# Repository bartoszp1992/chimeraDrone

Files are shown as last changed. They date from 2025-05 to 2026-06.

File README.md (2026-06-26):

# BD1 "Chimera" repo

**Chimera is 2,2" / 3" cinewhoop or freestyle type drone, for 3S/4S batteries, with fully 3D printed construction**

*Speed can be reduced in edgeTX system using logical switch based on the speed read from GNSS, and the mix function. The project includes a configuration that limits the speed when SB is UP*

## 3D printing

All on 0.4 brass nozzle, make sure you have at least 5 pieces- CF filaments will wear off quickly. Trim Z-offset after every CF print

I don't recommend using SS nozzle becouse it's too cold for my printer.

### tips/info
>please use proper materials. Drone components will be hot or very hot. Printing parts with PLA or similar will cause melt your construction during flight. **If my cheap Sidewinder X4 printer can handle this materials- yours printer also can.**

>It's not cheap project- don't do it because of lack of funds. Buying a ready frame will be cheaper than buying CF filaments

>one battery for one 2-3 minutes flight. Make sure you have more than 1

### parts
- **ducts**
: PA12. after print heat and bend down the wing trims by 90 degrees
- **frame**
: PC-CF/PETG-CF, 2 wall loops, no supports, 100% grid infill, rotate 15deg in Z axis
- **body**
: PA12
- **wings**
: any
- **roof**
: TPU A95
- **GNSS mount**
: TPU A95
- **Grip nuts, sleeves**
: PETG
- **top lock**
: PETG
- **light plate**
: TPU
- **bumper**
: PP
- **motor screw shim**
: PC

## BOM

### 3D printed
- 1 x ducts
- 1 x body
- 1 x frame
- 1 x left wing
- 1 x right wing
- 1 x roof or mount roof
- 1 x GNSS mount
- 1 x top lock
- 2 x camera sleeves
- 4 x sleeve 2mm
- 4 x sleeve 3mm
- 4 x grip nuts
- 1 x light plate
- 16 x 1.2mm sleeve for frame30
- 16 x 0.6mm sleeve for frame22

### electronic
- [ ] **FC**
: GEPRC TAKER G4 35A AIO
>you can use any other 35A+, compatible with 3/4S and 25,5mm pitch
- [ ] **propellers 2.2"**
: GEMFAN 2218 3-blade / HQprop 2216 3-blade (1.5mm shaft)
- [ ] **motors 2.2"**
: BETAFPV Lava series 1104 7200KV
- [ ] **propellers 3"**
: HQPROP T3X1.8X3 / HQPROP T3X3
- [ ] **motors 3"**
: flyfishRC FLASH 1404 4500KV
- [ ] **receiver**
: SpeedyBee Nano 2.4G ExpressLRS ELRS Receiver
>or any other ELRS receiver which can fit into modules mounts in body
- [ ] **camera**
: CADDX Ratel Pro
- [ ] **VTX analog**
: TBS Unify Pro32 Nano 5G8
- [ ] **VTX digital**
: BETAFPV P1 Air unit
- [ ] **battery 2.2"**
: LAVA 3S 550mAh 75C
- [ ] **battery 3"**
: LAVA II 4S 680mAh 95C
- [ ] **GNSS**
: Foxeer M10Q-180 compass- mount on **right** fame spoke, faced antenna up and socket left(to body)
- [ ] **Controller**
: RM Pocket, or any other with ELRS and edgeTX
- [ ] **Goggles**
: BETAFPV VR03 or any other analog goggles
- [ ] **VRX antenna**
: Any RHCP antenna
- [ ] **Charger**
: iMax B6 V2 with some 12V supplier / ToolkitRC Q4AC
- [ ] **5A car fuse and cable socket**
: charging fuse
- [ ] **4x RGB LED**
: if you want make night flies
- [ ] **2 x additional XT30 connectors set**
: to connect battery to charger and FC
- [ ] **red and black 18AWG silicon wire cables**
: to make connection with FC
- [ ] **25-30A car fuse and cable socket**
: not necessary, but recommended
- [ ] **14x9x5 (diameter * hole * height) ferrite ring**
: turn 3-4x GNSS cable as close as possible to GNSS modulestabilizer

### mechanical

- [ ] 1x 10x130mm battery velcro strap
- [ ] 8x 20mm M2 screws with barrel head for stack mount, and wing mount
>make sure you have spares- these screws can bend after hard landing :joy:
- [ ] 4x 10mm M2 screws with barrel head for body mount
- [ ] 12x M2 H3 D3.6mm brass insert
>you can recover it from broken parts, but make sure you have spares
- [ ] 4x M2 1,6mm nut to lock stack screws
- [ ] 4x M2 20mm PA screws to mount digital VTX
- [ ] 4x M2 0,8mm nut to screw in digital VTX
- [ ] 16x M2 8mm screws for frame30
- [ ] 16x M2 10mm screws for frame30 with motor screw shims
- [ ] 16x M2 6mm screws for frame22

## electronics
project contains configuration for HD version with BZ- pin used as VTX power switch. Implementation below:
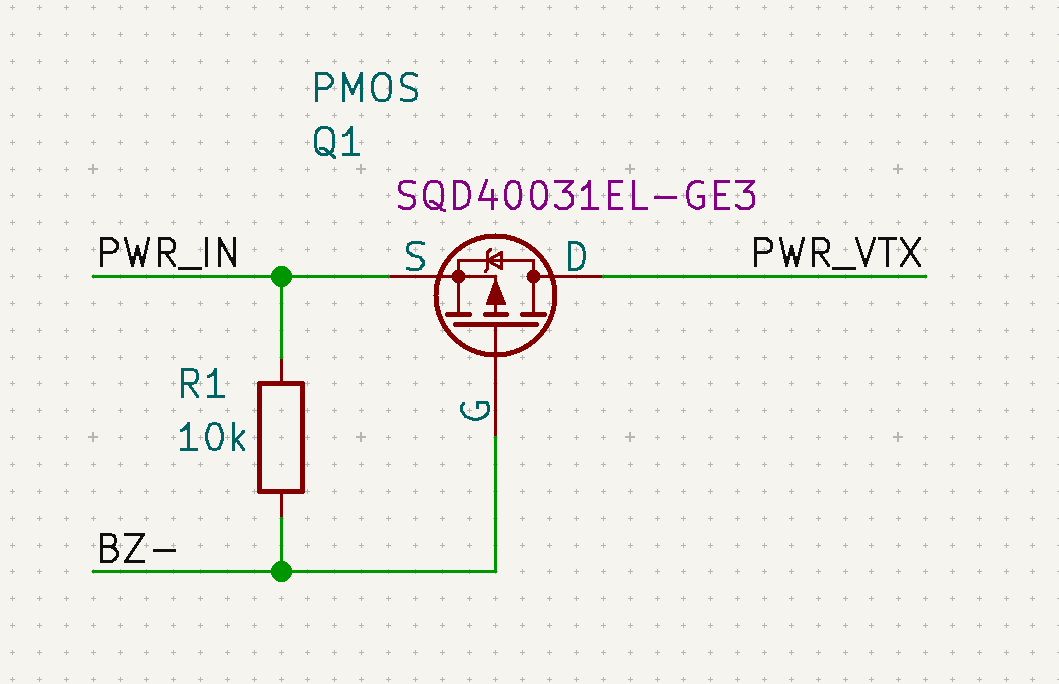
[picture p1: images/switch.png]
VTX power switch


## firmware
If you are building remotely:
> choose analog OSD Protocol and type **OSD_HD** in custom defines, to build firmware with both- digital and analog OSD 
> In other options add **Magnetometers**, **Position Hold** and **Altitude Hold**

**Thanks Baro for PID tunes!!**

Firmware notice

This repository may include firmware binaries and configuration files for flight controllers and ESCs.

Betaflight firmware is licensed under the GNU General Public License v3.0 (GPL-3.0).
Source code is available at: https://github.com/betaflight/betaflight

Bluejay ESC firmware is an open-source project.
Source code is available at: https://github.com/bird-sanctuary/bluejay

All respective rights belong to the original authors.
This repository does not claim ownership of these projects and only redistributes unmodified binaries for convenience.

*BD1 stands for "Bart's Design 1"*

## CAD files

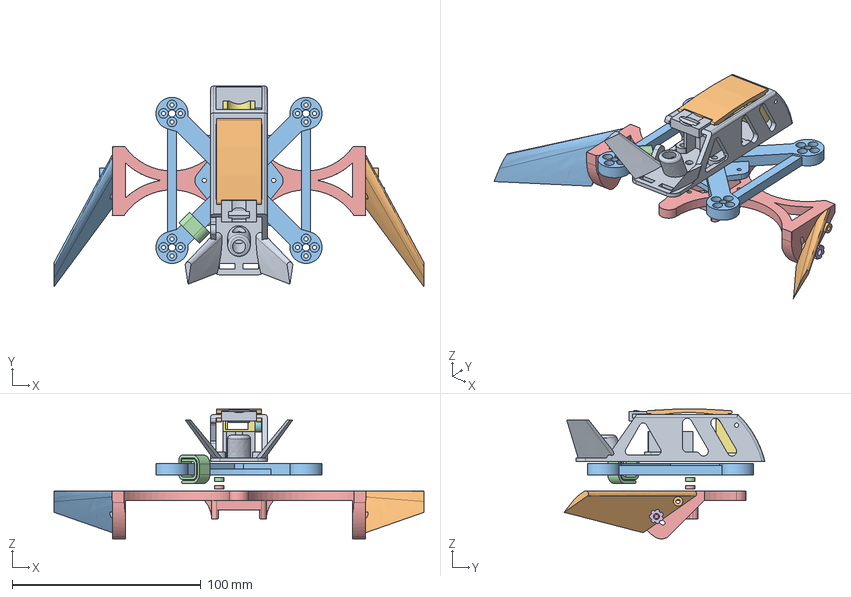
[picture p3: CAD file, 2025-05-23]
frame/fd.FCStd
196.0 x 106.4 x 68.8 mm
wing standalone
wing standalone mirror
FC top sleeve
FC bottom sleeve
grip nut
cam mount
cam trim sleeve
cable lock
roof
frame FDM2
cable mount
anti-duct

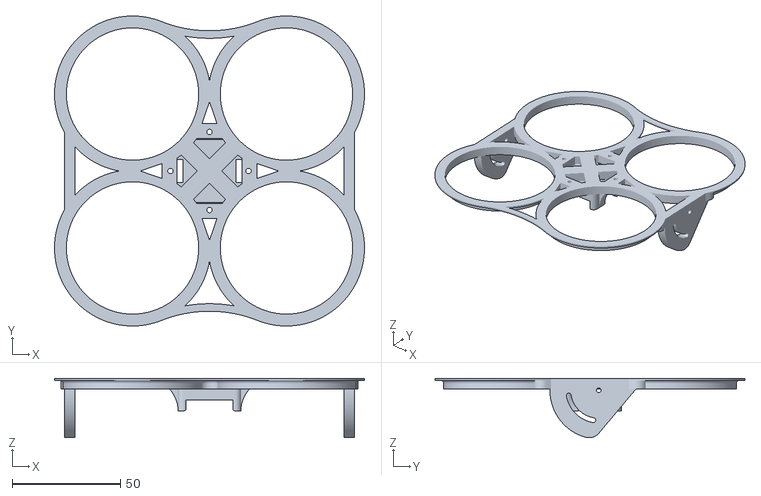
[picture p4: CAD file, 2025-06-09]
frame/output/parts_printer-duct-light.stl
143.0 x 143.0 x 27.4

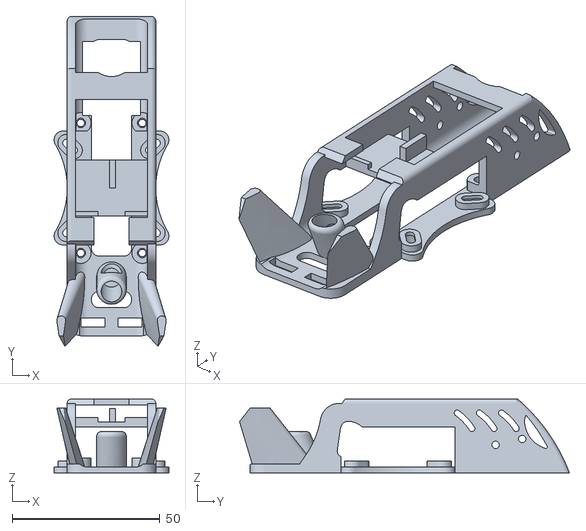
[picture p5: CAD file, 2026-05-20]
mechanical/output/parts_drone-body-SD_HD.stl
38.8 x 111.6 x 25.0

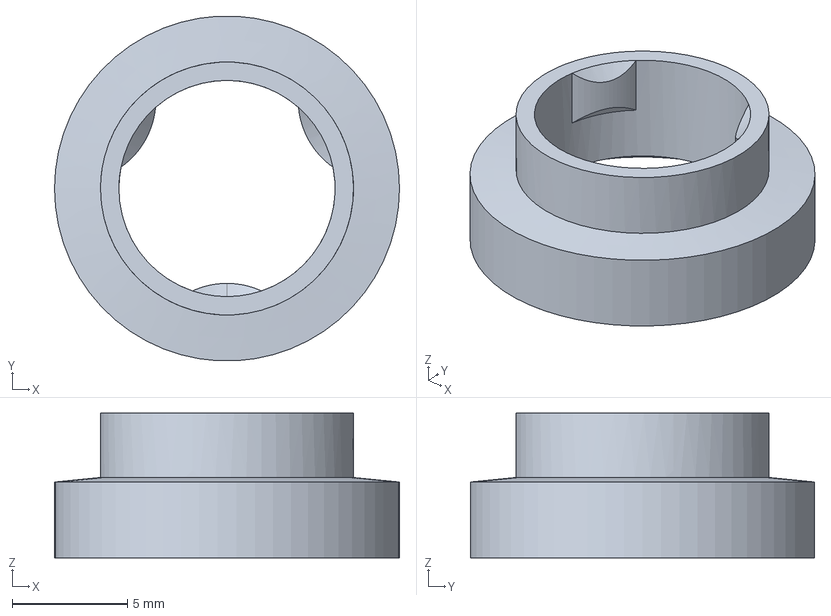
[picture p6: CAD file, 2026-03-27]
mechanical/parts/parts_P1.FCStd
15.0 x 15.0 x 6.30 mm

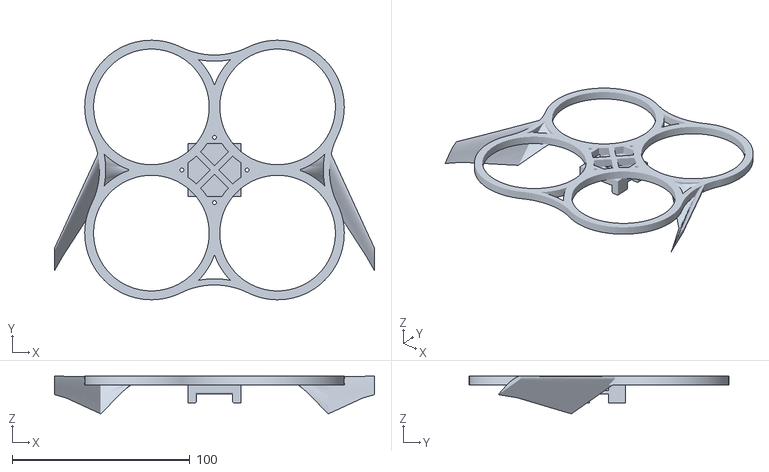
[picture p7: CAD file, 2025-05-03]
frame/output/fd-propeller cover.stl
180.0 x 146.0 x 21.2

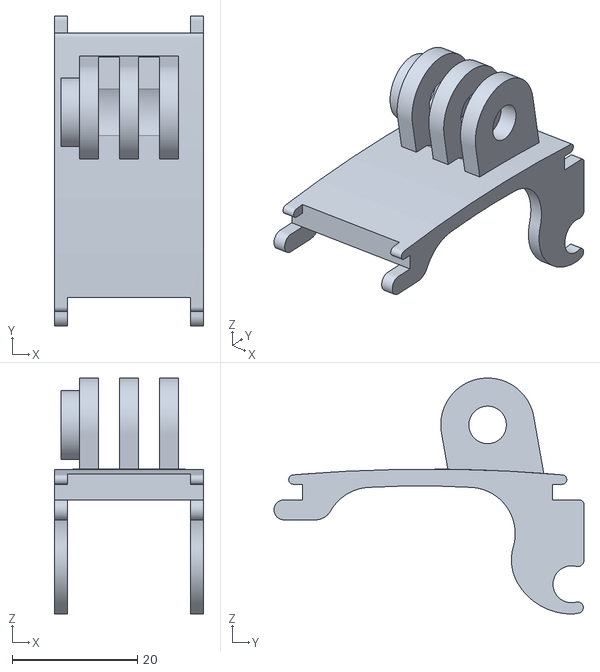
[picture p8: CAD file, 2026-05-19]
mechanical/output/parts_drone-mount roof.stl
23.9 x 49.6 x 37.7

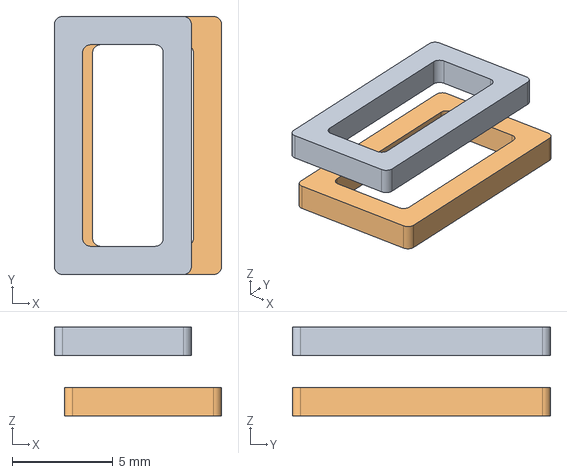
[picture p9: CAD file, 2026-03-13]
mechanical/parts/parts_strapDD.FCStd
8.30 x 12.8 x 4.40 mm
external
internal

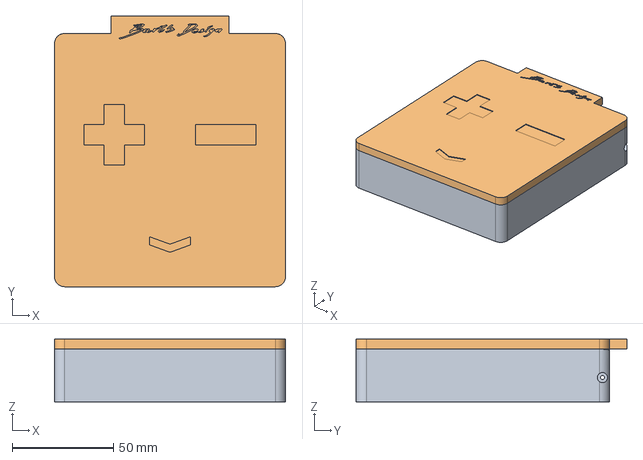
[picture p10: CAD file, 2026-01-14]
mechanical/parts/parts_batt_box.FCStd
114.0 x 133.5 x 31.0 mm
lid

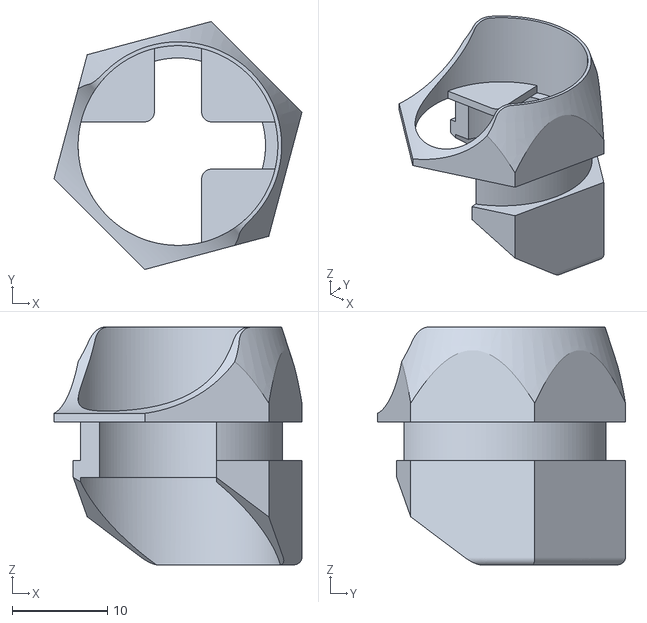
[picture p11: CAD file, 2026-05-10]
mechanical/output/parts_drone-bumper30.stl
26.1 x 26.1 x 25.0

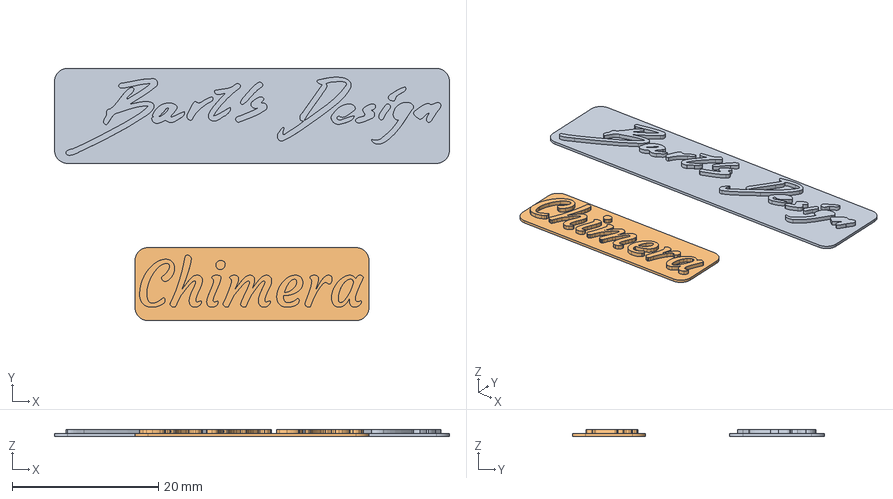
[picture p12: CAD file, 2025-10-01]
mechanical/parts/parts_labels.FCStd
54.0 x 34.5 x 1.00 mm
Bart's design-S
Chimera-S

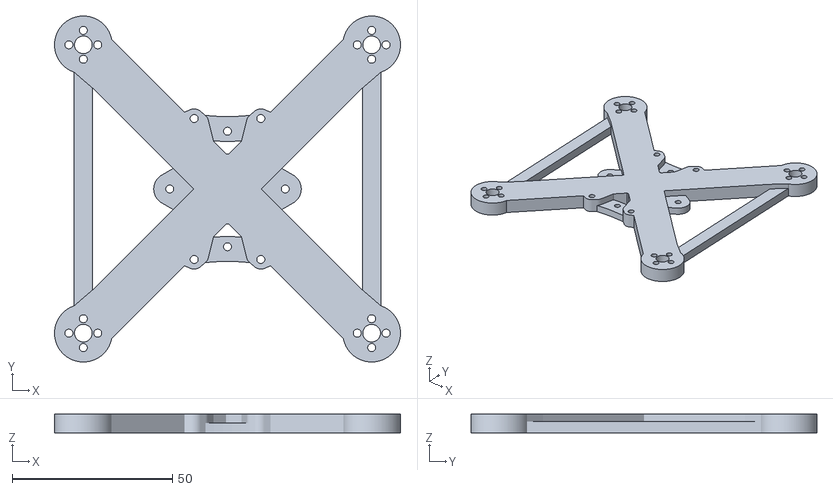
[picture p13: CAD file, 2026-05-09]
mechanical/output/parts_drone-frame30-R.stl
108.0 x 108.0 x 5.80

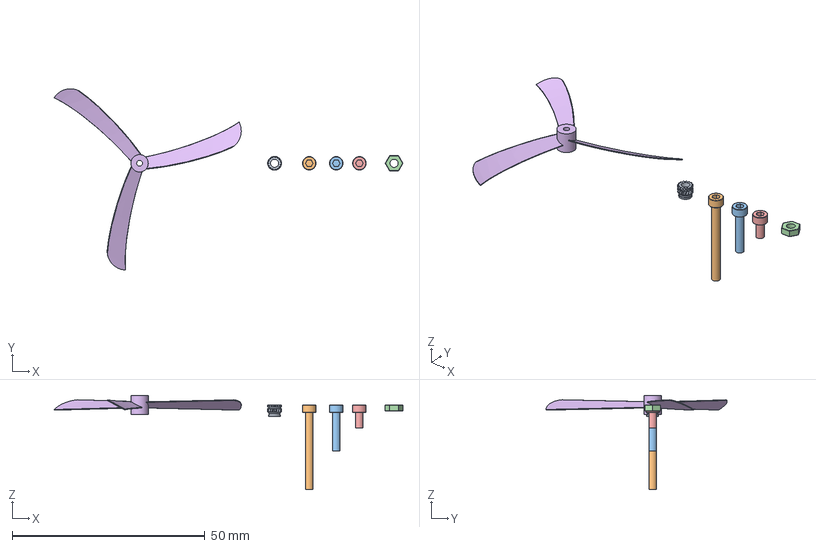
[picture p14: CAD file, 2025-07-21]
mechanical/parts/parts_mechanical.FCStd
90.5 x 47.0 x 24.5 mm
insert M2x6 D3.6mm
bolt M2x20mm
bolt M2x10mm
nut M2x1.6mm
bolt M2x4mm
propeller

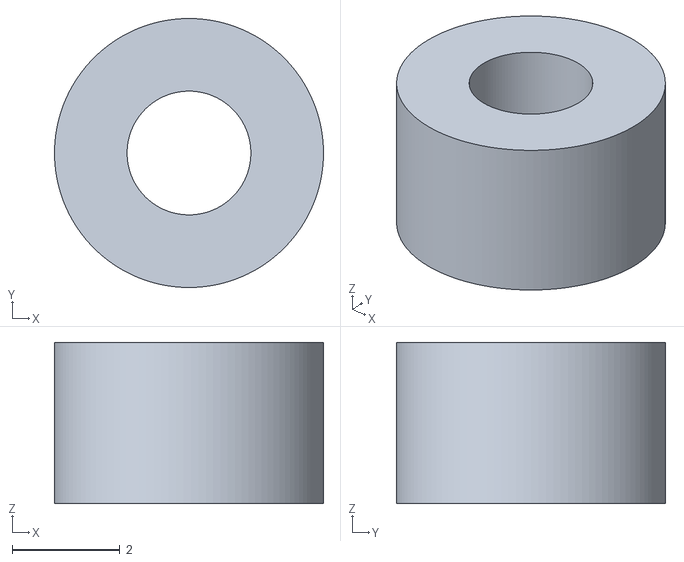
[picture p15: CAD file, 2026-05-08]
mechanical/output/parts_drone-sleeve 3mm.stl
5.00 x 5.00 x 3.00

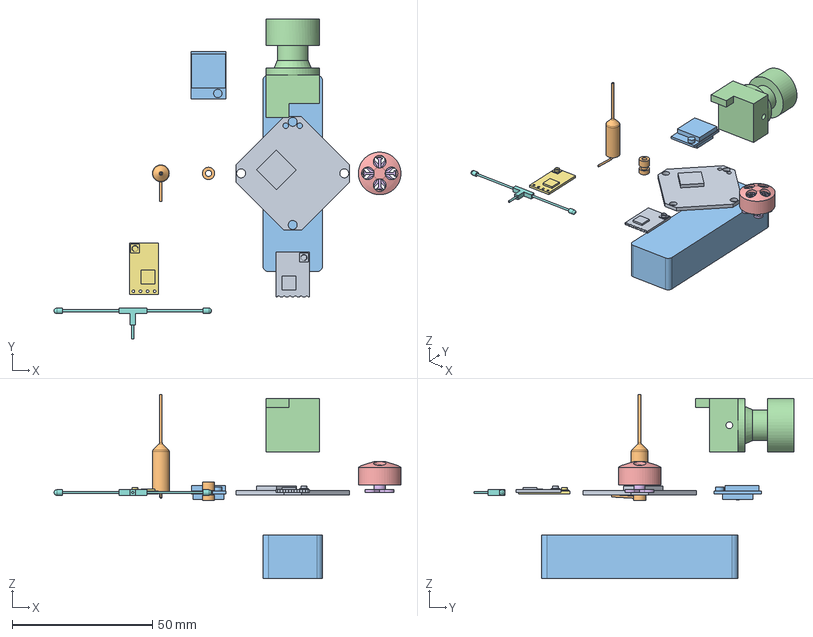
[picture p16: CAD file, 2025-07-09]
mechanical/parts/parts_electronic.FCStd
123.7 x 114.0 x 65.7 mm
flight controller
damper
battery
cam1919
rotor
stator
receiver
rx ant
VTX
VTX ant
GNSS

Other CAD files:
mechanical/output/parts_drone-sleeve 2mm.stl
mechanical/output/parts_drone-foot30.stl
mechanical/output/parts_drone-roof.stl
mechanical/output/parts_drone-light plate.stl
mechanical/output/parts_P1-cover.stl
mechanical/output/parts_P1-guard.stl
mechanical/output/parts_P1-standard lens adapter.stl
mechanical/output/parts_batt_box-box.stl
mechanical/output/parts_batt_box-lid.stl
mechanical/output/parts_drone-GNSS mount.stl
mechanical/output/parts_drone-VTX adapter.stl
mechanical/output/parts_drone-bottom30.stl
mechanical/output/parts_drone-cam trim sleeve1414.stl
mechanical/output/parts_drone-cam trim sleeve1919.stl
mechanical/output/parts_drone-ducts30.stl
mechanical/output/parts_drone-frame22.stl
mechanical/output/parts_drone-frame30.stl
mechanical/output/parts_drone-grip nut.stl
mechanical/output/parts_drone-motor screw shim.stl
mechanical/output/parts_drone-sleeve 0.6mm.stl
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

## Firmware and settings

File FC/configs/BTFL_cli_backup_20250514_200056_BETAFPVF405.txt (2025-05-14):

# diff all defaults

# version
# Betaflight / STM32F405 (S405) 4.3.1 Jul 13 2022 / 03:32:11 (8d4f005) MSP API: 1.44
# config: manufacturer_id: BEFH, board_name: BETAFPVF405, version: edcd244b, date: 2022-06-29T02:24:46Z

# start the command batch
batch start

# reset configuration to default settings
defaults nosave

board_name BETAFPVF405
manufacturer_id BEFH
mcu_id 002300283133510c34383739
signature 

# name: BD1 "Chimera"
#feature -GPS
#feature -TELEMETRY

# feature
feature -RX_PARALLEL_PWM
feature GPS
feature TELEMETRY
#feature RX_PARALLEL_PWM

# serial
#serial 0 0 115200 57600 0 115200
serial 0 2 115200 115200 0 115200
#serial 3 0 115200 57600 0 115200
serial 3 1 115200 57600 0 115200
#serial 5 0 115200 57600 0 115200
serial 5 8192 115200 57600 0 115200

# led
#led 0 0,0::C:0
led 0 12,12::C:1
#led 1 0,0::C:0
led 1 13,12::C:1
#led 2 0,0::C:0
led 2 14,12::C:1
#led 3 0,0::C:0
led 3 15,12::C:1
#led 4 0,0::C:0
led 4 12,13::C:1
#led 5 0,0::C:0
led 5 13,13::C:1
#led 6 0,0::C:0
led 6 14,13::C:1
#led 7 0,0::C:0
led 7 15,13::C:1
#led 8 0,0::C:0
led 8 12,14::C:1
#led 9 0,0::C:0
led 9 13,14::C:1
#led 10 0,0::C:0
led 10 14,14::C:1
#led 11 0,0::C:0
led 11 15,14::C:1
#led 12 0,0::C:0
led 12 12,15::C:1
#led 13 0,0::C:0
led 13 13,15::C:1
#led 14 0,0::C:0
led 14 14,15::C:1
#led 15 0,0::C:0
led 15 15,15::C:1

# aux
#aux 0 0 0 900 900 0 0
aux 0 0 0 1300 2100 0 0

# master
#set acc_calibration = 0,0,0,0
set acc_calibration = 9,-36,35,1
#set serialrx_provider = SBUS
set serialrx_provider = CRSF
#set bat_capacity = 0
set bat_capacity = 550
#set ibata_scale = 400
set ibata_scale = 240
#set yaw_motors_reversed = ON
set yaw_motors_reversed = OFF
#set osd_vbat_pos = 234
set osd_vbat_pos = 2464
#set osd_flymode_pos = 234
set osd_flymode_pos = 2490
#set osd_ah_pos = 78
set osd_ah_pos = 2158
#set osd_current_pos = 234
set osd_current_pos = 2496
#set osd_craft_name_pos = 234
set osd_craft_name_pos = 2541
#set osd_gps_speed_pos = 234
set osd_gps_speed_pos = 2522
#set osd_gps_lon_pos = 234
set osd_gps_lon_pos = 2065
#set osd_gps_lat_pos = 234
set osd_gps_lat_pos = 2097
#set osd_gps_sats_pos = 234
set osd_gps_sats_pos = 2048
#set osd_compass_bar_pos = 234
set osd_compass_bar_pos = 2054
#set osd_altitude_pos = 234
set osd_altitude_pos = 18937
#set osd_warnings_pos = 14665
set osd_warnings_pos = 14633
#set osd_avg_cell_voltage_pos = 234
set osd_avg_cell_voltage_pos = 416
#set osd_pit_ang_pos = 234
set osd_pit_ang_pos = 397
#set osd_battery_usage_pos = 234
set osd_battery_usage_pos = 2528
#set osd_disarmed_pos = 234
set osd_disarmed_pos = 2314
#set osd_esc_rpm_pos = 234
set osd_esc_rpm_pos = 0
#set osd_stat_battery = OFF
set osd_stat_battery = ON
#set vtx_band = 5
set vtx_band = 0
#set vtx_channel = 8
set vtx_channel = 0
#set vtx_power = 1
set vtx_power = 0
#set vtx_freq = 5917
set vtx_freq = 0
#set name = -
set name = BD1 "Chimera"

profile 0

profile 1

profile 2

# restore original profile selection
profile 0

rateprofile 0

rateprofile 1

rateprofile 2

rateprofile 3

rateprofile 4

rateprofile 5

# restore original rateprofile selection
rateprofile 0

# save configuration
save

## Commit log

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2025-05-03 add internal cover fillet
    [fd-propeller cover.stl, fd.FCStd]
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2025-05-03 simpler wing profile, thicker motor mounts
    [fd.FCStd]
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2025-05-03 frame fix, and center pocket
    [fd-duct wingless.stl, fd-frame.stl, fd-motor mount arraymotor mount.stl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]
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2025-05-07 add connections and firmwares
    [BTFL_CLI_BETAFPVF405 20A V5.txt, fd-frame.stl, fd.FCStd]
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2025-05-08 new colord in frame model
    [CNC pcb-B_Cu.gbr, CNC pcb-B_Mask.gbr, CNC pcb-B_Paste.gbr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]
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2025-05-09 exported frame and duct
    [fd-duct wingless.stl, fd-frame CNC.stl, fd.FCStd]
2025-05-09 add FDM frame, remove unnecessary holes, add sleeve
    [fd-sleeve.stl, fd.FCStd]
2025-05-09 more robust FDM frame
    [fd-frame FDM.stl, fd-sleeve 2mm.stl, fd-sleeve 3mm.stl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]
2025-05-09 larger motor mounts in FDM frame
    [fd-frame FDM.stl, fd.FCStd]
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2025-05-10 add VTX antenna mount
    [fd-body.stl, fd.FCStd]
2025-05-12 fixed body
    [fd-body.stl, fd.FCStd]
2025-05-12 body redesigned
    [chimeraConn.kicad_sch, fd-body.stl, fd.FCStd]
2025-05-12 body redesigned 2
    [fd.FCStd]
2025-05-12 add screw holes in body
    [fd-cable lock.stl, fd-cam trim sleeve.stl, fd.FCStd]
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2025-05-13 bigger camera mount sleeve, shorter roof
    [fd.FCStd]
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2025-05-14 add photo, fixed BOM
    [BTFL_cli_backup_20250514_200056_BETAFPVF405.txt]
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2025-05-14 shorter roof
    [fd-cable lock.stl, fd-roof.stl, fd.FCStd]
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2025-05-16 swapped uarts
    [BD1_Chimera_BTFL_BETAFPVF405-swap.txt, fd-roof.stl, fd.FCStd]
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2025-05-17 more robust duct center
    [fd.FCStd]
2025-05-17 removed fillet on up side of duct
    [fd.FCStd]
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2025-05-19 add stl for new frame
    [fd-frame FDM2.stl]
2025-05-20 more robust battery mount
    [fd.FCStd]
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2025-05-22 looser cable mount
    [3dprint.3mf, fd-cable mount.stl]
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2025-05-23 new cable mounts on 3d printer table
    [3dprint.3mf]
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2025-05-23 new 3d print file
    [3dprint.3mf]
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2025-05-24 more robust body, larger max wing angle
    [3dprint.3mf, fd-anti-duct.stl, fd-body.stl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]
2025-05-24 fixed stabilizer base
    [3dprint.3mf, fd-body.stl]
2025-05-26 better wing angle, cut for tool in duct
    [3dprint.3mf, BD1_Chimera_BTFL_BETAFPVF405-swap.txt, fd-anti-duct wingless.stl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]
2025-05-26 update schematic and BOM
    [chimeraConn.kicad_sch]
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2025-05-30 add gopro mount, clear PID settings, new controller model presets
    [BD1_Chimera_BTFL_BETAFPVF405-swap.txt, fd-mount roof.stl]
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2025-05-30 stl export, 3d print file update
    [fd-roof.stl]
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2025-05-31 looser cam mount
    [3dprint.3mf, fd-cam mount.stl]
2025-05-31 body reinforcement
    [3dprint.3mf, fd-body.stl]
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2025-06-03 removed unnecessary reinforcements in body, fixed duct-light
    [3dprint.3mf, fd-body1919.stl, fd-duct-light.stl]
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2025-06-04 fix mount roof, add case
    [3dprint.3mf, fd-cam trim sleeve1919.stl, fd-case bottom.stl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]
2025-06-04 new frame, new body mount holes positions
    [3dprint.3mf, fd-body1919.stl, fd-frame FDM.stl]
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2025-06-05 add portable case bottom
    [case.FCStd]
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2025-06-06 add readme instead of BOM
    [fd-duct-light.stl]
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2025-06-07 updated case lid output, updated 3d print file
    [3dprint.3mf, fd-case lid.stl]
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2025-06-07 grip position fix
    [assembly.FCStd]
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2025-06-07 assembly with receiver antenna
    [assembly_body.FCStd, assembly_frame.FCStd, assembly_motor.FCStd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]
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2025-06-07 working on main assembly
    [assembly_body.FCStd, assembly_controller.FCStd, assembly_duct.FCStd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]
2025-06-07 some assembly errors to fix
    [assembly_body.FCStd, assembly_controller.FCStd, assembly_duct.FCStd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]
2025-06-09 new FC pitch restructured FC folder add new in todo regenerated stl files add alternative FC
    [3dprint.3mf, BD1_Chimera_BTFL_BETAFPVF405-swap.txt, BTFL_CLI_BETAFPVF405 20A V5.txt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]
2025-06-09 stop tracking backup files
    [assembly_body.FCStd, assembly_controller.FCStd, assembly_duct.FCStd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]
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2025-06-09 case base fix latch on hinge case assembly
    [assembly_case.FCStd, parts_case.FCStd]
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2025-06-10 add betafpv FC firmware
    [3dprint.3mf, BTFL_CLI_BETAFPVF405 20A V5.txt, BTFL_cli_backup_20250610_230253_BETAFPVF405.txt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]
2025-06-10 auto-land failsafe
    [BD1_Chimera_BTFL_BETAFPVF405-swap.txt]
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2025-06-12 new piece of drone
    [3dprint.3mf, BD1_Chimera_BTFL_BETAFPVF405-swap.txt, chimeraConn.kicad_sch]
2025-06-13 smaller duct mount holes in frame
    [3dprint.3mf, parts_printer-frame FDM.stl]
2025-06-13 2,2mm motor mount holes
    [3dprint.3mf, parts_printer-frame FDM.stl]
2025-06-13 case fix
    [3dprint.3mf, parts_case-case base.stl, parts_case-case latch.stl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]
2025-06-13 save 3mf and xcf
    [3dprint.3mf]
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2025-06-17 update auto-land add SA as requirement for speed alarm
    [BD1_Chimera_BTFL_BETAFPVF405-swap.txt]
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2025-06-20 readme update case update
    [3dprint.3mf, parts_case-case base.stl, parts_case-case lid.stl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]
2025-06-21 larger GNSS pocket in lid
    [3dprint.3mf, parts_case-case lid.stl, parts_case.FCStd]
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2025-07-04 fix mesh on Bart's Design label
    [3dprint.3mf, parts_labels-Bart's design.stl, parts_labels.FCStd]
2025-07-07 lighter frame and duct
    [assembly_frame.FCStd, parts_printer-frame FDM.stl]
2025-07-07 remove case new body
    [3dprint.3mf, assembly_case.FCStd, assembly_main.FCStd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]
2025-07-08 small fixes
    [3dprint.3mf, parts_case-case base.stl, parts_case-case latch.stl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]
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2025-07-09 frame assembly for MkII
    [assembly_frame.FCStd]
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2025-07-09 assembly for Mk II
    [assembly_body.FCStd, assembly_controller.FCStd, assembly_duct.FCStd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]
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2025-07-14 rename FC config for MKI update speed limit settings in Chimera model
    [BD1_Chimera_BTFL_BETAFPVF405-MkI.txt]
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2025-07-21 wings corrections
2025-07-21 stl and 3d print file update
    [3dprint.3mf, parts_printer-left wing.stl, parts_printer-right wing.stl]
2025-07-21 right wing as separate body
    [assembly_duct.FCStd, assembly_grip_nut.FCStd]
2025-07-21 longer wing tip cross-section
    [assembly_body.FCStd, assembly_controller.FCStd, assembly_duct.FCStd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]
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2025-07-21 more smooth wing cut
    [3dprint.3mf, parts_printer-left wing.stl, parts_printer-wing main.stl]
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2025-09-10 Add new single profile, with speed limit set on SB
    [BD1_Chimera_BTFL_BETAFPVF405-MkIII.txt]
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2025-09-15 add large wings remove Chimera edgeTX model, add FPV model remap arm to SB
    [BD1_Chimera_BTFL_BETAFPVF405-MkIII.txt, parts_printer-wing LL.stl, parts_printer-wing LR.stl]
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2025-10-03 add failsafe switch
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2025-10-27 video changed for NTSC, remove betafpv FC configs
    [BD1_Chimera_BTFL_BETAFPVF405-MkI.txt, BD1_Chimera_BTFL_BETAFPVF405-MkII.txt, BD1_Chimera_BTFL_BETAFPVF405-MkIII-poshold-beta.txt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]
2025-11-15 fix power values
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2025-12-29 body and mount roof fixes
    [parts_printer-body1919-2.stl, parts_printer-mount roof1919.stl]
2026-01-05 mmono buttons swapped
2026-01-05 vtx power revert
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2026-01-24 body fixes for P1
    [3dprint.3mf, parts_printer-body1919-3.stl]
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2026-02-07 change crash flip switch
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2026-02-10 crash flip switch changed in SD config
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2026-02-21 disabled crash flip and magnetometer
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2026-02-26 logical switches fix
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2026-03-01 restore stiffer ducts
    [parts_printer-wing LL.stl, parts_printer-wing LR.stl]
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2026-03-16 remove anti ducts, ducts and frame rename to 22
    [parts_printer-anti-ducts.stl, parts_printer-frame FDM.stl, parts_printer-frame22.stl]
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2026-03-17 VTX mount fix
    [parts_printer-body-SD_HD.stl]
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2026-03-19 bottom corrections
    [parts_printer-bottom30.stl]
2026-03-20 bottom nut fix wireless trainer add 3inch cli
    [parts_printer-bottom30.stl]
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2026-03-21 frame30 fix
    [parts_printer-frame30.stl]
2026-03-22 light plate redesigned
    [parts_printer-light plate.stl]
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2026-03-25 lens cover update, battery changed to lava II
    [parts_P1-cover.stl, parts_P1.FCStd]
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2026-03-26 add reinforcements
    [parts_printer-bottom30.stl]
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2026-03-28 name fix
    [parts_printer-wing ML.stl, parts_printer-wing MR.stl, parts_stapDD-external.stl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]
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2026-04-21 fix cli files
    [8=VTX-CONFIG.txt]
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2026-05-08 bumper fix, add prop screw distance
    [parts_drone-bumper30.stl, parts_prop_screw_distance-distance.stl, parts_prop_screw_distance.FCStd]
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2026-05-20 reinforced body
    [parts_drone-body-SD_HD.stl]
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2026-05-20 Revert "add LFS"
    This reverts commit 59e303863db83eafd04d799c17953a8605207b34.
    [parts_P1-cover.stl, parts_P1-guard.stl, parts_P1-standard lens adapter.stl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]
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
